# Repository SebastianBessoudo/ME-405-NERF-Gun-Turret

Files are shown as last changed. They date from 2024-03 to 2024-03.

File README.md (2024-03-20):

# ME-405-NERF-Gun-Turret
Calpoly ME 405 Class term project in building a NERF gun turret that can auto-fire on a target
## Authors:
Sebastian Bessoudo and Nathaniel Davis
## Introduction
The goal of this project is to design an autonomous NERF gun turret that detects and tracks a target and fires a projectile. For the tournament, the launcher must turn 180 degrees with a motor and align itself using an infrared camera to face and hit the target within 10 seconds.  There must also be an emergency shutdown button that can be pushed or a red exposed wire that can be pulled  to stop the automation of the turret at any time. 
## Hardware Design
Our design comprises four wooden blocks supporting a slender 3D-printed component below a Lazy Susan. This Susan is linked to a laser-cut wooden piece equipped with a rail attachment for the NERF gun and an additional compartment designed to house the servo for trigger firing. The underside of the 3D-printed component securely fastens the front section of a DC motor (37d 50-70 encoder), while its tip connects to the laser-cut wooden piece, facilitating rotation of the upper system via the Lazy Susan mechanism. The rail attachment accommodates the NERF gun and also features a dedicated compartment for a torque servo motor positioned at a higher level to engage the trigger mechanism. Rubber bands are employed to secure all components in place to prevent the servo motor from dislodging. The wooden blocks, 3D-printed pieces, and the lower section of the Lazy Susan are firmly fastened together with screws, while the upper portion is assembled using nuts and bolts for added stability. Additionally, an 'L'-shaped metal prop away from the assembly to support the infrared camera in place.
### Assembly Drawing
CAD_assembly_nerfgun
### Physical Design
nerfgun_fullview
nerfgun_closeup
## Software Design
The software for this project is a cooperative multitasking system that contains three tasks: a mastermind task, a motor control task, and a camera task.

The mastermind task in charge of running the main code instructs what the turret is supposed to do in its movement, alignment, triggering, and shooting of the projectile. It also configures the intertask variables ir_angle and motor_setpoint for the utilization of the other tasks.

The motor control task uses the intertask variable motor_setpoint to have the motor rotate in a certain direction and setpoint. It is used for moving the motor in the phase of turning the turret 180 degrees and its alignment toward the target. 

The camera task takes a snapshot from an infrared camera and prints a CSV image that shows numbers based on the intensity of the heat signature. It also reads the CSV image and computes ir_angle for the direction of the highest intensity (or numbers) for the alignment of the turret.
### Task Diagram
taskdiagram
### FSM for Mastermind
state_diagram
### FSM for task 2 and task 3
state_diagram1

See a full description of our software in the link to our repository: [ Github Page](https://sebastianbessoudo.github.io/ME-405-NERF-Gun-Turret/)
## Testing
Each test served as a preparatory phase for the final design. Initially, our focus was on testing the motor's ability to rotate to the designated setpoint upon button activation. We verified this by leveraging our encoder class to provide precise motor position feedback.

We then proceeded to evaluate the performance of the infrared camera using mlx_cam.py to ensure it captured the necessary images accurately. Upon confirmation, our attention shifted to assessing the camera's ability to capture multiple snapshots while concurrently coordinating with the motor through main.py.

Following successful tests on motor-camera coordination, we examined the system's ability to align the motor based on camera feedback and initiate the NERF gun projectile launch via servo motor triggering. Though most tests yielded positive results, we encountered challenges with the servo motor's functionality.

Specifically, we encountered difficulties with the MG995 servo motor, which proved unsuitable for our project due to several factors. These included its excessive current requirement of 1.2A, surpassing our project's 0.5A limit from the DC power supply, instances of unintended continuous rotation, and frequent overshooting of designated setpoints. These issues collectively hindered the servo motor's ability to reliably perform its intended function of pulling the NERF gun trigger.
## Lessons Learned and Final Recommendations
The primary takeaway from our project was the critical importance of careful electronics selection. The MG995 servo motor posed challenges because of its inability to consistently and accurately rotate to the designated setpoint. It also caused unexpected computer shutdowns when connected to the Nucleo during testing.

The issue stemmed from the servo motor attempting to draw excessive current from the computer while both were linked to the Nucleo. Consequently, whenever we executed the code, the computer repeatedly shut down. To avoid such complications in the future, it's essential to opt for either an alternative gear motor or a servo motor with the appropriate current requirements.

For instance, the HXT900 micro servo emerges as a promising alternative. It not only meets the project's current requirements but also offers reliability. Although it possesses lower torque compared to the MG995 servo motor, which is crucial for triggering the NERF gun, crafting a mechanism with the servo motor to engage the trigger remains a viable and potentially successful approach.

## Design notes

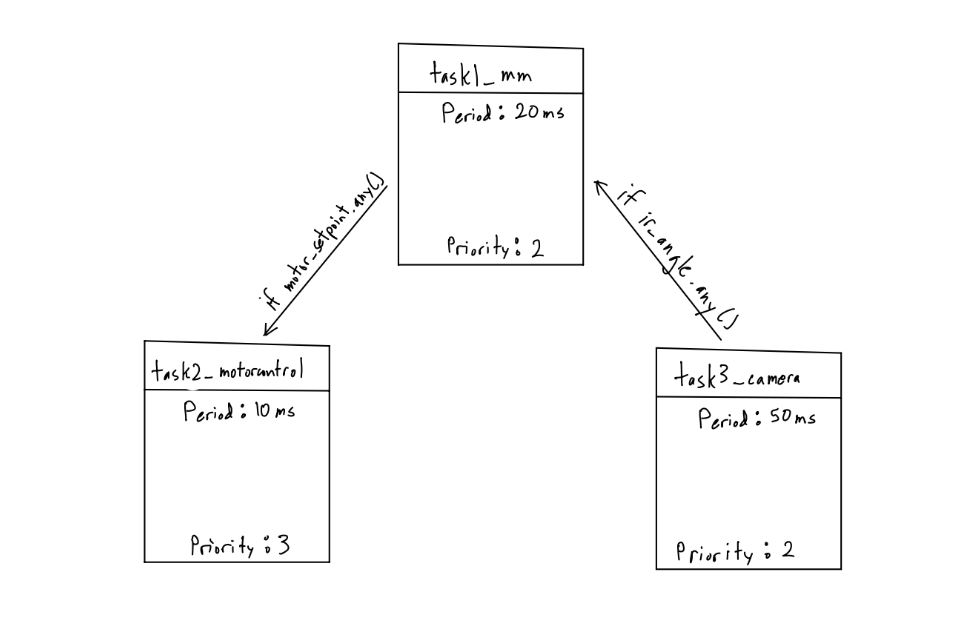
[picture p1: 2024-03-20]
images/taskdiagram.JPG

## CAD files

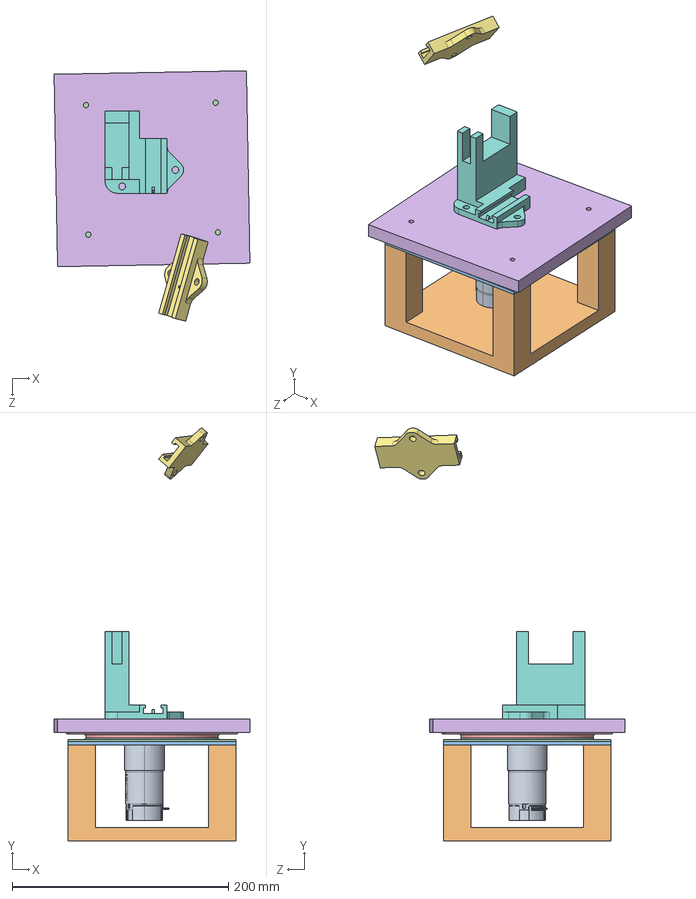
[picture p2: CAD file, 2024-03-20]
CAD/NerfTurret.SLDASM
181.0 x 381.5 x 231.4 mm
37d-gearmotor-50-70-encoder.step
Housing Bottom
Motor Mount
Lazy Susan_1a
Lazy Susan_1b
Housing Top
Rail Clip
Rail Clip With Servo v2

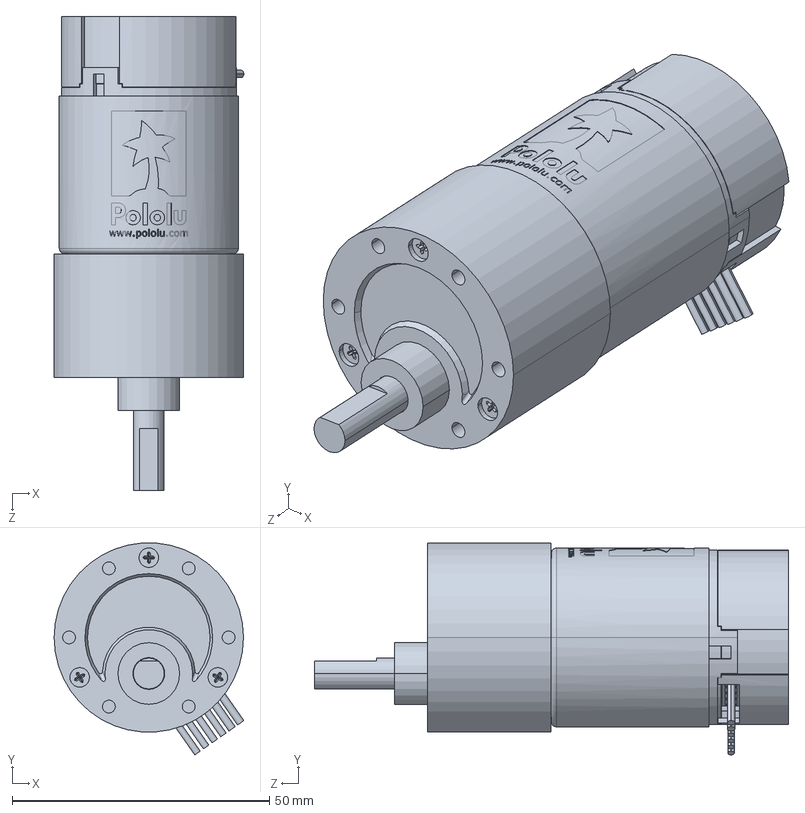
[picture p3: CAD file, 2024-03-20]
CAD/37d-gearmotor-50-70-encoder.step.SLDPRT
36.9 x 41.2 x 92.1 mm

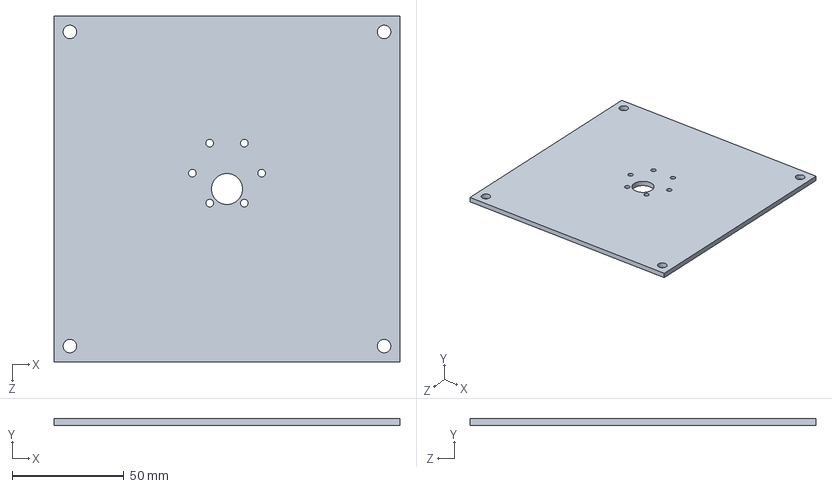
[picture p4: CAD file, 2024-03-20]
CAD/Motor Mount.SLDPRT
154.9 x 3.17 x 154.9 mm

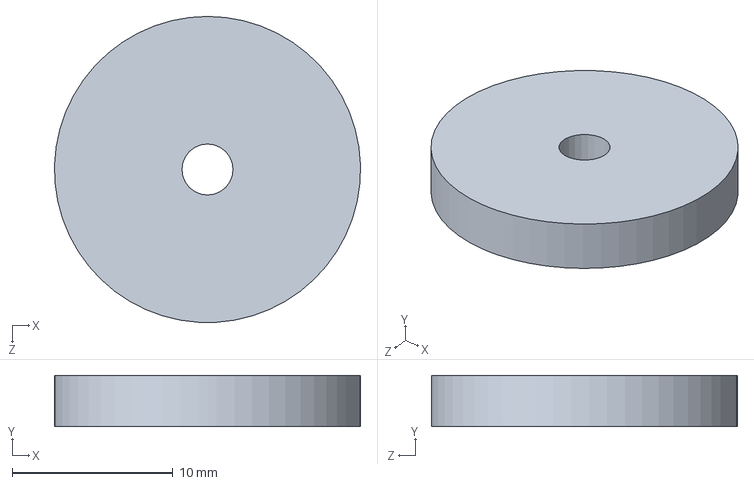
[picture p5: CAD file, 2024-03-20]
CAD/servo ext.SLDPRT
19.0 x 3.17 x 19.1 mm

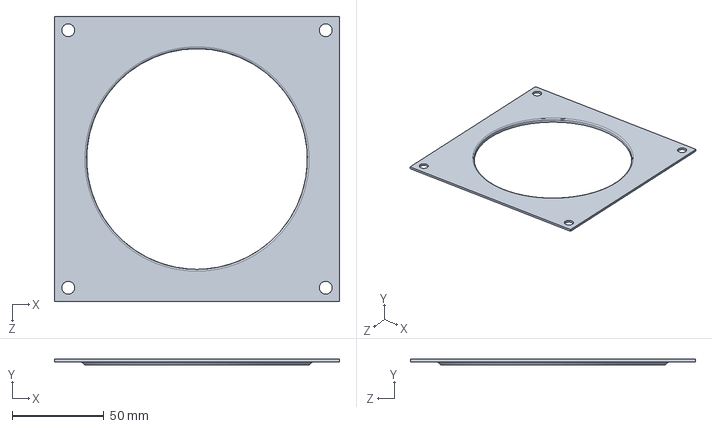
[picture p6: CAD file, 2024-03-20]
CAD/Lazy Susan_1a.SLDPRT
155.0 x 3.00 x 155.0 mm

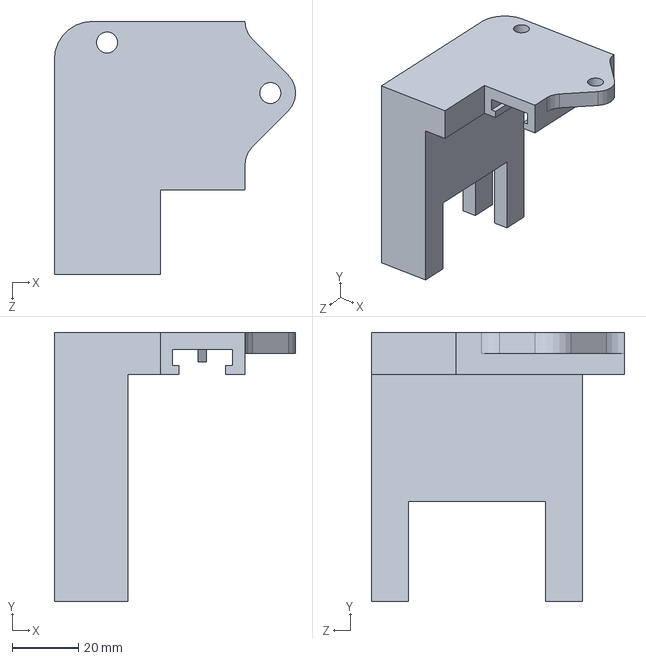
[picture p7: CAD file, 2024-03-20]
CAD/Rail Clip With Servo v2.SLDPRT
72.6 x 81.0 x 76.2 mm

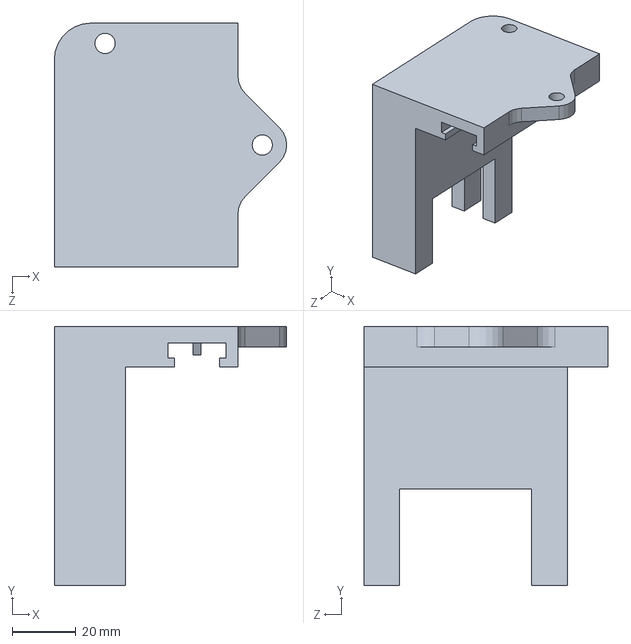
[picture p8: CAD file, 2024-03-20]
CAD/Rail Clip With Servo.SLDPRT
72.6 x 81.0 x 76.2 mm

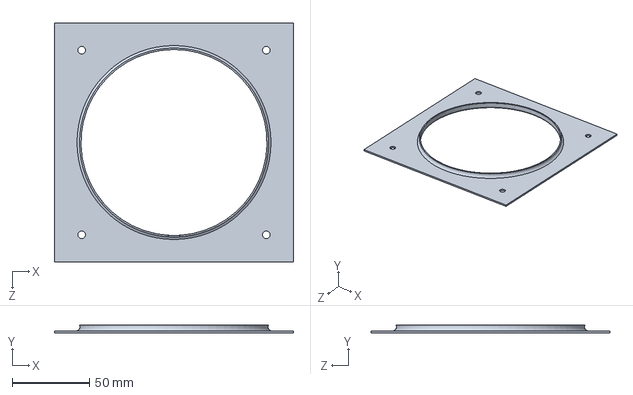
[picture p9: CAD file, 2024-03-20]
CAD/Lazy Susan_1b.SLDPRT
155.0 x 5.00 x 155.0 mm

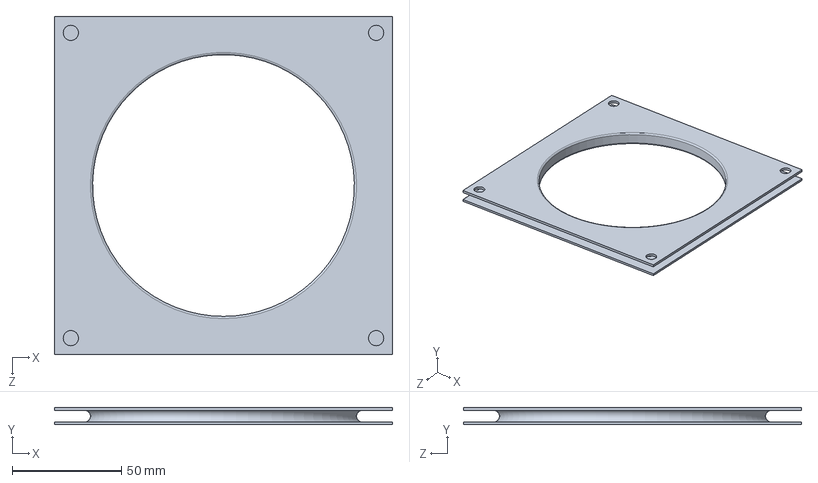
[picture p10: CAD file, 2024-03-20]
CAD/Lazy Susan.SLDPRT
155.0 x 8.00 x 155.0 mm

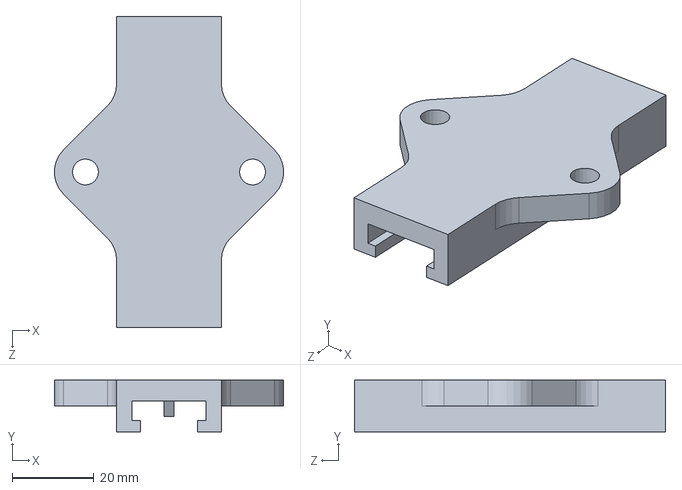
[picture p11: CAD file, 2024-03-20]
CAD/Rail Clip.SLDPRT
56.0 x 12.7 x 76.2 mm

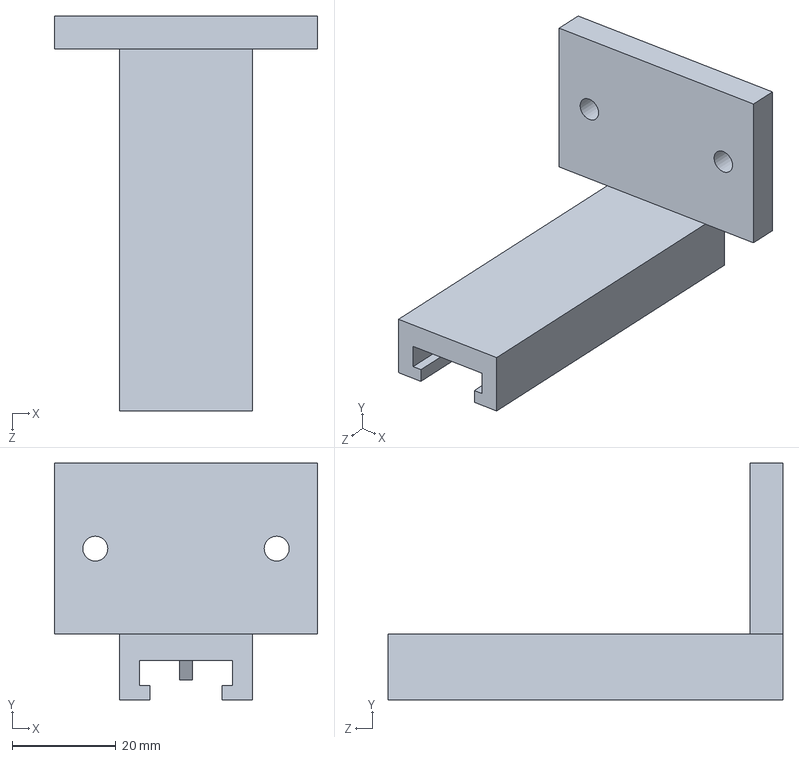
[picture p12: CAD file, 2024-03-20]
CAD/Rail Clip For IR Cam.SLDPRT
50.8 x 45.7 x 76.2 mm

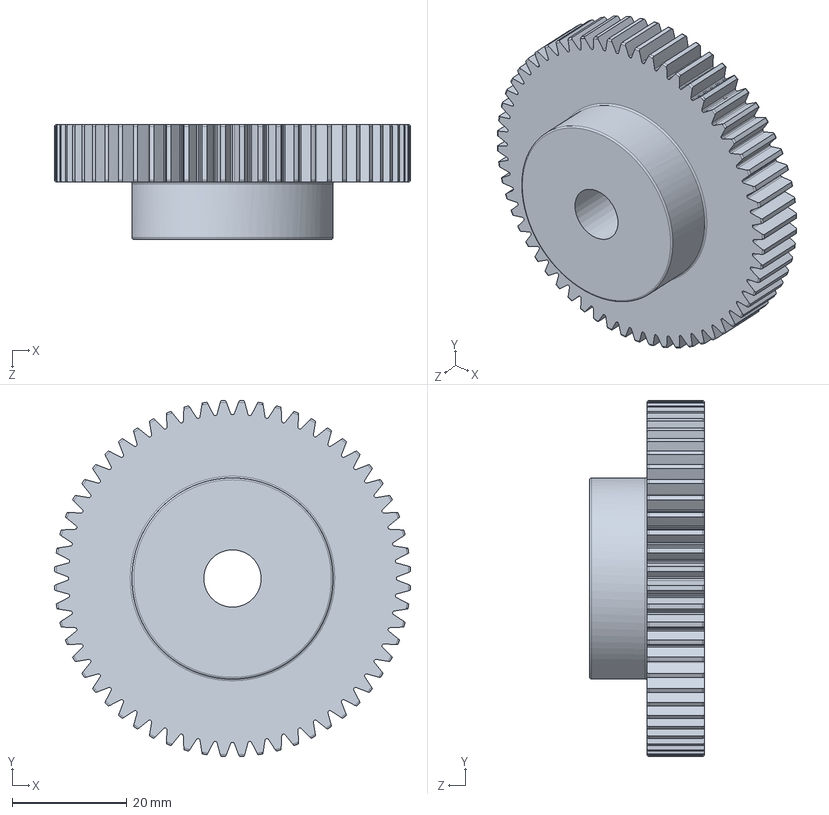
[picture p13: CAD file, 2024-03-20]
CAD/2662N435_20 Degree Pressure Angle Plastic Gear.SLDPRT
62.0 x 62.0 x 20.0 mm

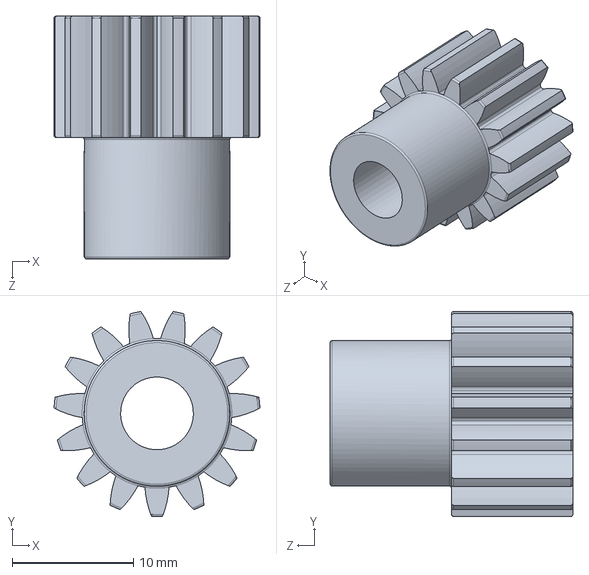
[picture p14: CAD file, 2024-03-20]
CAD/2662N415_20 Degree Pressure Angle Plastic Gear.SLDPRT
17.0 x 16.9 x 20.0 mm

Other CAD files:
CAD/Housing Top.SLDPRT
CAD/Housing Bottom.SLDPRT
CAD/37d-gearmotor-50-70-encoder.step

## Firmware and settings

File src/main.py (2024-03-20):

"""! @file main.py
Term Project of Nathaniel Davis and Sebastian Bessoudo.
When the blue button on the Nucleo is pressed, its start the firing process
of turning around 180 degrees, aligning itself using an infrared camera,
and fires a projectile towards the intended target
@author Nathaniel Davis
@author Sebastian Bessoudo
@date 3-12-24
"""

import pyb
import gc
import pyb
import cotask
import task_share
from motor_driver_updated import MotorDriver
from encoder_reader_updated import Encoder 
from motorwithencoder_updated import MotoEncodo
from servo import Servo
from mlx_cam import MLX_Cam
import math
import time
from machine import Pin, I2C
from mlx90640 import MLX90640
from mlx90640.calibration import NUM_ROWS, NUM_COLS, IMAGE_SIZE, TEMP_K
from mlx90640.image import ChessPattern, InterleavedPattern


def task1_mm(shares):
    """!
    The mastermind of main.py that instructs the process of what all the electronics are supposed to do.
    Uses the intertask variables ir_angle and motor_setpoint to cotask with task2_motorcontrol and
    task3_camera.
    """
    S0_INIT = 0
    S1_BUTTON = 1 
    S2_TURN = 2
    S3_CAM = 3
    S4_MOTOR = 4
    S5_FIRE = 5
    S6_RESET = 6

    state = S0_INIT
    
    while True:
        ir_angle, motor_setpoint = shares
        if(state == S0_INIT): # initializes system            
            # set up servo
            servpin = pyb.Pin.board.PB6
            servtimer = 4
            servchannel = 1
            serv = Servo(servpin, servtimer, servchannel)

            
            # set up flywheel output
            flypin = pyb.Pin.board.PC3
            flywheel = pyb.Pin(flypin, pyb.Pin.OUT_PP)
            flywheel.low()
            
            #set up button pin
            buttonpin = pyb.Pin.board.PC13
            button = pyb.Pin(buttonpin, pyb.Pin.IN)
            
            state = S1_BUTTON
            yield
            
        elif(state == S1_BUTTON): # waits for button press
            if button.value():
                state = S2_TURN
            yield
        elif(state == S2_TURN): # turns 180 degrees and waits 6 seconds
            print("turning")
            motor_setpoint.put(1600)
            time.sleep(6)
            
#             for _ in range(600):
#                 time.sleep_us(1000)
#                 yield
            state = S3_CAM
            yield
        elif(state == S3_CAM): # takes the currently stored camera info
            print("checking camera")
            if ir_angle.any():
                angle = ir_angle.get()
                state = S4_MOTOR
                yield
        elif(state == S4_MOTOR): # moves motor
            print("adjusting")
            if ir_angle.any():
                setpoint = motor_setpoint.get()
                setpoint -= angle*16
                motor_setpoint.put(setpoint)
                state = S5_FIRE
            yield
        elif(state == S5_FIRE): # fire away!
            print("firing!")
#             flywheel.high() # start flywheel motors
#             for _ in range(2000):
#                 time.sleep_us(1000)
#             servo.set_angle(142)
#             for _ in range(1000):
#                 time.sleep_us(1000)
#             flywheel.low()
#             servo.set_angle(100)
#             time.sleep_ms(500)
#             servo.off()
            state = S6_RESET
            yield
        elif(state == S6_RESET): # resets system
            motor_setpoint.put(0)
            yield
        
def task2_motorcontrol(shares):
    """!
    This task uses the motor controller that constantly attempts to
    reach the setpoint set in the intertask variable "motor_setpoint".
    """
    S0_INIT = 0
    S1_UPDATE_MOTOR = 1
     
    state = S0_INIT
    while True:
        ir_angle, motor_setpoint = shares
        if(state == S0_INIT):
            # motor pins
            mtrAplus = pyb.Pin.board.PB4
            Aplusch = 1
            mtrAminus = pyb.Pin.board.PB5
            Aminusch = 2
            mtrEN = pyb.Pin.board.PA10
            mtrtimer = 3

            # encoder pins
            encA = pyb.Pin.board.PC6
            encAch = 1
            encB = pyb.Pin.board.PC7
            encBch = 2
            readch = 8
            
            # set up motor driver
            moe = MotorDriver(mtrEN, mtrAplus, Aplusch,  mtrAminus, Aminusch, mtrtimer)
            # set up encoder
            enc = Encoder(encA, encB, readch, encAch, encBch)
            # set up motor control
            motorctrl = MotoEncodo(moe, enc)
            motorctrl.set_Kp(1)
            
            state = S1_UPDATE_MOTOR
            yield
            
        elif(state == S1_UPDATE_MOTOR):
            if motor_setpoint.any():
                setpoint = motor_setpoint.get()
                motorctrl.set_setpoint(setpoint)
                motor_setpoint.put(setpoint)
                print(f'setpoint: {setpoint}, current location: {enc.read()}')
            yield
        
def task3_camera(shares):
    """!
    This task constantly updates the intertask variable "ir_angle"
    with an angle of greatest heat signature.
    """
    S0_INIT = 0
    S1_UPDATE_CAMERA = 1
    
    state = S0_INIT
    while True:
        ir_angle, motor_setpoint = shares
        if(state == S0_INIT):
            import gc
            # The following import is only used to check if we have an STM32 board such
            # as a Pyboard or Nucleo; if not, use a different library
            try:
                from pyb import info

            # Oops, it's not an STM32; assume generic machine.I2C for ESP32 and others
            except ImportError:
                # For ESP32 38-pin cheapo board from NodeMCU, KeeYees, etc.
                i2c_bus = I2C(1, scl=Pin(22), sda=Pin(21))

            # OK, we do have an STM32, so just use the default pin assignments for I2C1
            else:
                i2c_bus = I2C(1)

            # Select MLX90640 camera I2C address, normally 0x33, and check the bus
            i2c_address = 0x33
            scanhex = [f"0x{addr:X}" for addr in i2c_bus.scan()]

            # Create the camera object and set it up in default mode
            camera = MLX_Cam(i2c_bus)
            camera._camera.refresh_rate = 1.0
            state = S1_UPDATE_CAMERA
            yield
        elif(state == S1_UPDATE_CAMERA):
            # Get an image and see how long it takes to grab that image
            # Keep trying to get an image; this could be done in a task, with
            # the task yielding repeatedly until an image is available
            image = None
            while not image:
                image = camera.get_image_nonblocking()
                yield
            # Can show image.v_ir, image.alpha, or image.buf; image.v_ir best?
            # Display pixellated grayscale or numbers in CSV format; the CSV
            # could also be written to a file. Spreadsheets, Matlab(tm), or
            # CPython can read CSV and make a decent false-color heat plot.
            csv = []
            for line in camera.get_csv(image, limits=(0, 99)):
                csv.append(sum([eval(i) for i in line.split(',')]))
                yield
            cam_row = csv.index(max(csv))
            angle = cam_row - 12.5
            ir_angle.put(angle) 
            gc.collect()
            yield
            
if __name__ == "__main__":
    
    # create intertask data here
    ir_angle = task_share.Queue('h', 1, thread_protect=True, overwrite=True, name="IR Angle")
    motor_setpoint = task_share.Queue('l', 1, thread_protect=True, overwrite=True, name="Motor Setpoint")
    
    # create tasks
    task1 = cotask.Task(task1_mm, name="Mastermind", priority=2, period=20, profile=True, trace=False, shares=(ir_angle, motor_setpoint))
    task2 = cotask.Task(task2_motorcontrol, name="Motor Control", priority=3, period=10, profile=True, trace=False, shares=(ir_angle, motor_setpoint))
    task3 = cotask.Task(task3_camera, name="Camera", priority=2, period=50,profile=True, trace=False, shares=(ir_angle, motor_setpoint))
    cotask.task_list.append(task1)
    cotask.task_list.append(task2)
    cotask.task_list.append(task3)
    
    # clean up memory
    gc.collect()
    
    # create scheduler
    while True:
        try:
            cotask.task_list.pri_sched()
        except KeyboardInterrupt:
            break
    
    
    

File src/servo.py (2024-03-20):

"""! @file servo.py
Servo controller class. Running as main will make servo rotate at specific speed.
@author Nathaniel Davis
@date 3-13-24
"""

import time
import pyb

class Servo:
    """!
    This class implements a servo controller to move to its designated setpoint and stop
    """
    def __init__(self, servpin, timer, ch):
        """
        Creates the servo controller using PWM
        @param servpin pin that the servo is connected to
        @param timer timer for the servo pin
        @param channel channel for the servo pin
        """
        servo_pin = pyb.Pin(servpin, pyb.Pin.OUT_PP)
        tim = pyb.Timer(timer, freq = 50) # period is 20 ms
        self.servo_channel = tim.channel(ch, pyb.Timer.PWM, pin = servo_pin)
    def cw(self):
        """
        Makes servo turn clockwise
        """
        self.servo_channel.pulse_width_percent(5)
    def ccw(self):
        """
        Makes servo turn counter-clockwise
        """
        self.servo_channel.pulse_width_percent(10)
    def off(self):
        """
        Turns servo off
        """
        self.servo_channel.pulse_width_percent(0)
        
    def stop(self):
        """
        Makes servo stop
        """
        self.servo_channel.pulse_width_percent(7.5)
    
if __name__ == "__main__":
    serv = Servo(pyb.Pin.board.PB6, 4, 1)
    firing = 220
    serv.ccw()
    time.sleep_ms(firing)
    serv.stop()
    time.sleep(0.5)
    serv.cw()
    time.sleep_ms(firing)
    serv.stop()
    time.sleep(0.5)
    serv.off()

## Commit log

2024-03-19 Update README.md with CAD assembly and physcial design
2024-03-20 CAD files
    [2662N415_20 Degree Pressure Angle Plastic Gear.SLDPRT, 2662N435_20 Degree Pressure Angle Plastic Gear.SLDPRT, 37d-gearmotor-50-70-encoder.step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]
